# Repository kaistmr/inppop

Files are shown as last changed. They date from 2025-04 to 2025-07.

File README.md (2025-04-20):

# 인형뽑기 repository
이는 2025년도 태석제 및 캄프를 위한 인형뽑기 제작을 위한 사이드 프로젝트이다.

## 멤버
- 전체 팀장: **노경민**
- 하드웨어 팀: **노경민**, 전재원, 김희태, 류호현, 김준홍, 이명제, 이지후, 정용환
- 전장 및 전산 팀: **안연수**, 전재원, 이지후, 송민준

## 플젝 기간
|기간|활동|
|--|--|
|2025.03.16.|내부 회의 및 플젝 시작|
|2025.04.22.|pcb 테스트 및 코딩 진행|
|2025.05.03.|하드웨어 제작 완료|
|2025.05.13.-15.|태울석림제에서 시연 진행|

## 안내사항
기존 2025년도에 제작하여 주문한 pcb에서는 아두이노 메가 프로 부분에서의 GND 통일이 되어있지 않았다는 실수를 발견하여, 이를 점퍼를 이용해서 이어줌.
추후 다시 만든 manufacturing 파일은 문제 없는 상태이지만 2025버전을 사용할 때는 이를 유의해야 함.

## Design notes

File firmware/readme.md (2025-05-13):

# Firmware
- 최종 사용 코드 : `ard_nano.ino`, `mega.ino`
- 중간중간에 요소들 테스트는 `./test_elements` 폴더 속 파일들을 이용.
- 참고로 못 쓰게 된 핀도 많으니까 유의해서 코드 보기.

## Arduino nano
### Distance Sensing
- 핀: A7과 D2핀을 사용.
- 센서: distance sensor 사용
- 목적: 동전 투입구에 사용. 거리값이 일정한 상태에서 거리값이 줄어들어 동전 투입이 인식되면 대기 시퀀스에서 게임 시작 시퀀스로 변경
- 예제 코드: `./test/distance_sensor_test`

### mp3 module
- 핀: D6과 D12를 이용해 rx, tx 통신을 사용
- 모듈: DFPlayer mini를 활용
- 작동:
  - 대기 시퀀스: 폴더 하나(A) 속 노래를 랜덤하게 재생. 이 과정에서 폴더 내부 노래는 무한 반복
  - 게임 시작 시퀀스: 다른 폴더(B) 내부의 노래를 순차적으로 재생. 폴더 내부 노래는 무한 반복
- 통신 방식:
  - 직접 시리얼 통신을 통한 제어
  - 10바이트 명령어 패킷 사용 (SOF, VI, DL, CMD, ACK, DH, DL, CHL, CHH, EOF)
  - 체크섬을 통한 데이터 무결성 검증
  - 주요 명령어:
    - 0x0F: 음악 재생
    - 0x06: 볼륨 설정
    - 0x0C: 모듈 리셋
  - 초기화 순서:
    1. 모듈 리셋
    2. 볼륨 설정
    3. 음악 재생 시작
- 예제 코드: `./test/mp3_test`

## Arduino mega
### motor control
- 1번 모터(x축)
  - 모터 종류: DC모터
  - 모터 연결 핀: Signal(D40), Motor Control(D36, D38)
- 2번 모터(y축)
  - 모터 종류: DC모터
  - 모터 연결 핀: Signal(D41), Motor Control(D37, D39)
  - **주의사항** : 이 핀들은 이미 만들어진 보드에서 작동하지 않음. 따라서 외부 L298N을 사용해야 함. 혹은 z축 핀을 y축에 활용하고 3번 모터는 서보모터를 활용하는 것도 방법... (쓴다면 D35 핀을 사용)
- 3번 모터(z축)
  - 모터 종류: DC모터
  - 모터 연결 핀: Signal(D46), Motor Control(D42, D44)
  - 제어 방식: L298N을 활용한 제어. 적당히 감고, 적당히 푸는 능력이 중요
- 4번 모터(그리퍼)
  - 모터 종류: servo모터
  - 모터 연결 핀: D34 핀을 이용한 제어
  - 제어 방식: 최소 각도와 최대 각도를 정하고, 이를 반복하는 방식
- 리밋스위치
  - D9, D11, D15, D17을 이용해 x축의 +-, y축의 +- 최대치를 판별, z축의 경우 D19을 이용.
  - **주의사항** : D13번 핀은 왜인지 모르겠지만 작동하지 않음. 따라서 이를 제외하고 사용해야 함!
- 예제 코드: `./test/limit_switch_test`, `./test/motor_only_test`

### control input
- 조이스틱: 리밋스위치가 총 4개인 버전. D23, D25, D27, D29를 통해 값이 들어오며, 이를 바탕으로 x, y 축 이동
- 푸쉬버튼:
  - D31을 통해 리밋스위치 방식으로 값이 들어옴.
  - 버튼이 눌릴 시 dc 모터로 z축을 내린 뒤, 그리퍼로 늘렸다가 오므린 뒤, 다시 z축을 높히고, 원점으로 이동 후 그리퍼 펼치기 작업 실행.
  - 이 버튼이 눌린다면 게임 종료 시퀀스로 돌입.
- 예제 코드: `./test/joystick_button_test`

## Signal Pin(mega and nano)
- 핀(nano): D8(DigitalWrite)과 D3(DigitalRead)을 사용
- 핀(mega): D3(DigitalRead)와 D5(DigitalWrite)을 사용
- nano의 D8과 mega의 D3, nano의 D3과 mega의 D5는 서로 이어져 있음.
- 작동:
  - 동전이 투입된 이후 게임 시작 시퀀스 돌입시, arduino nano의 D8의 state를 1로 세팅.
  - Arduino mega의 D3 쪽에서 이를 인식 후, Mega의 D5을 1로 세팅하여 게임을 진행.
  - 게임이 끝나면 mega의 D5 값이 0으로 바뀌며, mini의 D3핀이 연결된 핀이 0 값을 read.
  - D3 핀에서 0 값이 인식되면 D8의 값을 0으로 내리며 하나의 과정 종료.
  - 이를 반복

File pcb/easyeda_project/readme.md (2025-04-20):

# PCB files 수정사항

|날짜|제목|수정사항|
|--|--|--|
|2025.3월|1차 pcb 제작|최대한 범용성 넓게 쓰기 위한 것을 목표로 제작|
|2025.04.21.|GND 수정|아두이노 메가의 GND가 통일되어있지 않음을 발견하여 수정|

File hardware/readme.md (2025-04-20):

# Hardware
이 공간은 하드웨어 관련 설계 파일이 올라갈 예정입니다.

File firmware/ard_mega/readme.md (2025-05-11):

- 하고자 하는 방향이었지만, 뭔가 잘 안되는 거 때문에 인터럽트를 적게 사용하고, 하는 방향으로 수정.
- **여기 폴더의 코드는 사용하지 않습니다**

## 핀맵
### communication
- nano로부터의 receive: D3(interrupt)
- nano로의 send: D5
- 여기서 게임 기회: `coin`

### control
- x+: D23(PA1)
- x-: D25(PA3)
- y+: D27(PA5)
- y-: D29(PA7)
- push: D31, D3(interrupt)

### limit
- x+: D9(PH6)
- x-: D11(PB5)
- y+: D15(PJ0)
- y-: D17(PH0)
- z: D19(PD2)
- 닿았을 때 flag: `stop_motor_z`

### origin point
- `x- & y+` 위치
- 원점 이동하라는 flag: `gohome`

## logic(loop)
if(`grip`)
if(`gohome`)
joy to move

### joy to move
- joy 값을 read
- 이거를 (x+, x-, y+, y-)에 대한 값으로 변경
  - 0: move
  - 1: don't move
- limit에 대한 값도 동일하게 가져오기(닿으면 0)
- joy(x+, x-, y+, y-)와 limit(x+, x-, y+, y-)의 값을 각 파트에 대해서 not(joy) and limit 적용한 거를 최종 모터에 전달
- 전달 받은 값 (x+, x-, y+, y-) 에 대한 값을 모터에 적용해서 움직임 진행

### push to grip
- push 버튼의 값이 인식되면, 모든 움직임 멈추기, `grip` flag 를 변화

### gohome
- `gohome` flag 값이 1이면 실행하는 거
- 무조건 왼쪽 상단으로 움직이기
- 그리퍼 열고 닫기
- 리밋 스위치 값 다 들어오면 `gohome` flag를 0으로 되돌리기

### grip
- `grip` flag가 들어오면 실행
- 그리퍼 열고
- z축 내리고
- 그리퍼 닫고
- z축 리밋 닿을 때까지 올리고
- `gohome` flag 1로 변화
- 1 `coin` 사용하기

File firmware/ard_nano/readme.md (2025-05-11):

## arduino nano 코드 구조
1. 2개의 상태가 존재: 동전 대기 / 게임 진행
2. 동전 대기:
- mp3 모듈에서 1번 폴더 속 노래를 랜덤하게 반복 재생
- distance 센서 인식 중
- 신호를 송신 받는 8번 핀이 LOW로 설정
3. 동전 대기 -> 게임 진행
- distance 센서 인식(D2) ; 인터럽트
- D8을 HIGH로 설정
- 만약 D7에 값이 HIGH가 들어오면 게임 진행 시퀀스로 돌입
4. 게임 진행:
- mp3 모듈에서 2번 폴더 속 노래를 랜덤하게 반복 재생
- 지속적으로 D7 핀에서 신호 수신(defalt: HIGH)
5. 게임 진행 -> 동전 대기
- D7 핀에 LOW 신호가 수신되면 D8 핀의 값도 LOW로 설정
- 다시 동전 대기 시퀀스 돌입

### 노래 개수
- 1번 폴더: 001-134
- 2번 폴더: 001-084

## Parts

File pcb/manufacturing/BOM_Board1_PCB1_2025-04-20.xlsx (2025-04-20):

No. | Quantity | Comment | Designator | Footprint | Value | Manufacturer Part | Manufacturer | Supplier Part | Supplier
1 | 1 | 100nF | C1 | CAP-SMD_L3.2-W1.6-RD | 100nF | CA45-A-35V-0.1UF-K | CEC(振华新云) | C2976900 | LCSC
2 | 2 | 220nF | C2,C3 | C0603 | 220nF | CC0603JRX7R6BB224 | YAGEO(国巨) | C519555 | LCSC
3 | 1 | 100nF | C4 | C0603 | 100nF | C0603X104K050T | IHHEC(禾伸堂) | C187860 | LCSC
4 | 2 | 220uF | C5,C6 | CAP-TH_BD8.0-P3.50-D0.6-FD | 220uF | HG1H227M0816PC | HONOR(荣誉) | C5438873 | LCSC
5 | 3 | BM04B-GHS-TBT(LF)(SN) | CN3,CN4,CN26 | CONN-SMD_4P-P1.25_BM04B-GHS-TBT-LF-SN |  | BM04B-GHS-TBT(LF)(SN) | JST | C161692 | LCSC
6 | 16 | BM02B-GHS-TBT(LF)(SN) | CN5,CN6,CN10,CN13,CN14,CN15,CN16,CN17,CN18,CN19,CN20,CN21,CN22,CN23,CN24,CN25 | CONN-SMD_2P-P1.25_BM02B-GHS-TBT-LF-SN |  | BM02B-GHS-TBT(LF)(SN) | JST | C161690 | LCSC
7 | 3 | KF141R-2.54-3P | CN7,CN27,CN28 | CONN-TH_3P-P2.54_KF141R-2.54-3P |  | KF141R-2.54-3P | KEFA(科发) | C475125 | LCSC
8 | 6 | KF141R-2.54-2P | CN8,CN9,CN31,CN32,CN33,CN34 | CONN-TH_2P-P2.54_KF141R-2.54-2P |  | KF141R-2.54-2P | KEFA(科发) | C475124 | LCSC
9 | 1 | XT60PW-M | CN35 | CONN-TH_XT60PW-M |  | XT60PW-M | AMASS(艾迈斯) | C98732 | LCSC
10 | 2 | DB141R-2.54-12P-GN | CN36,CN37 | CONN-TH_12P-P2.54_DIBO_DB141R-2.54-12P |  | DB141R-2.54-12P-GN | DORABO(地博电气) | C2898763 | LCSC
11 | 16 | 1N5819WS | D9,D10,D11,D12,D13,D14,D15,D16,D17,D18,D19,D20,D21,D22,D23,D24 | SOD-323_L1.8-W1.3-LS2.5-RD |  | 1N5819WS | Hottech(合科泰) | C191023 | LCSC
12 | 2 | PZ254V-11-22P | H1,H2 | HDR-TH_22P-P2.54-V-M |  | PZ254V-11-22P | XFCN(兴飞) | C22465881 | LCSC
13 | 2 | PZ254V-11-16P | H3,H4 | HDR-TH_PZ254V-11-16P |  | PZ254V-11-16P | XFCN(兴飞) | C22465876 | LCSC
14 | 1 | 2Ω | R1 | R0603 | 2Ω | SCR0603J2R | VO(翔胜) | C3017797 | LCSC
15 | 2 | 47kΩ | R2,R3 | R0603 | 47kΩ | 0603WAJ0473T5E | UNI-ROYAL(厚声) | C25600 | LCSC
16 | 2 | 10kΩ | R4,R5 | R0603 | 10kΩ | AT0603BRD0710KL | YAGEO(国巨) | C723396 | LCSC
17 | 1 | ARDUINO_NANO | U1 | COMM-TH_ARDUINO_NANO |  | ARDUINO_NANO |  | C9900017879 | LCSC
18 | 1 | DFplayer | U6 | DFplayer
19 | 1 | 1000uF | U7 | CAP-TH_BD12.5-P5.00-D0.6-FD | 1000uF | 35YXF1000MEFC12.5X25 | rubycon(红宝石) | C439893 | LCSC
20 | 1 | TDA7297 | U8 | MULTIWATT-15_L19.6-W5.0-P1.27-L |  | TDA7297 | ST(意法半导体) | C96009 | LCSC
21 | 1 | 10uF | U9 | CAP-SMD_BD4.0-L4.3-W4.3-LS5.0-FD | 10uF | VT10UF16V167RV0128 | KNSCHA(科尼盛) | C5246581 | LCSC
22 | 2 | PZ254V-11-15P | U10,U11 | HDR-TH_15P-P2.54-V-M |  | PZ254V-11-15P | XFCN(兴飞) | C22465875 | LCSC
23 | 1 | 470uF | U12 | CAP-SMD_BD6.3-L6.6-W6.6-LS7.2-FD | 470uF | RST470UF10V029 | KNSCHA(科尼盛) | C4747954 | LCSC
24 | 1 | ARD_MEGA2560PRO | U13 | COMM-SMD_L54.0-W38.0-P2.54_ARD_MEGA2560PRO |  | ARD_MEGA2560PRO |  | C9900135944 | LCSC
25 | 2 | L298N | U14,U15 | MULTIWATT-15_L19.6-W5.0-P1.27-L |  | L298N | ST(意法半导体) | C19922 | LCSC
26 | 2 | KH-SS22D07-VG4H | U16,U17 | SW-TH_KH-SS22D07-VG4H |  | KH-SS22D07-VG4H | kinghelm(金航标) | C5274482 | LCSC

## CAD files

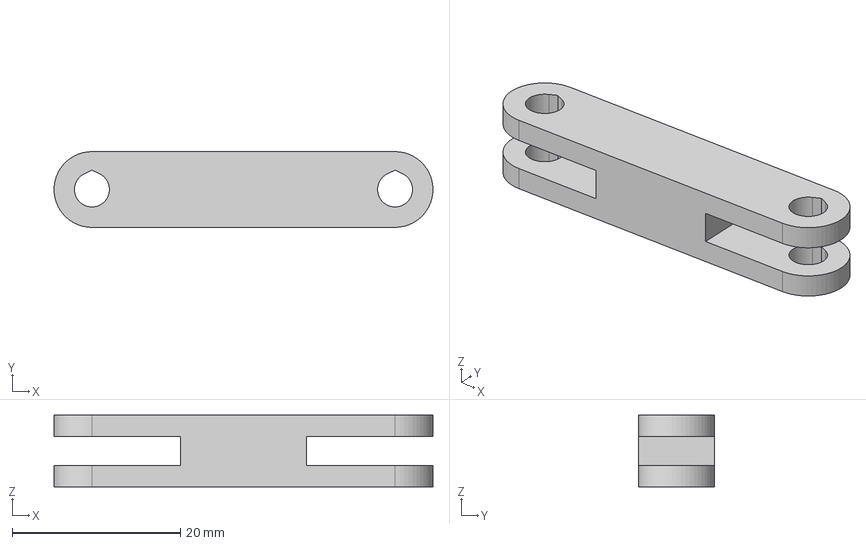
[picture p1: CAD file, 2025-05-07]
hardware/Claw STEP files/Part H v6.step
45.0 x 9.00 x 8.50 mm

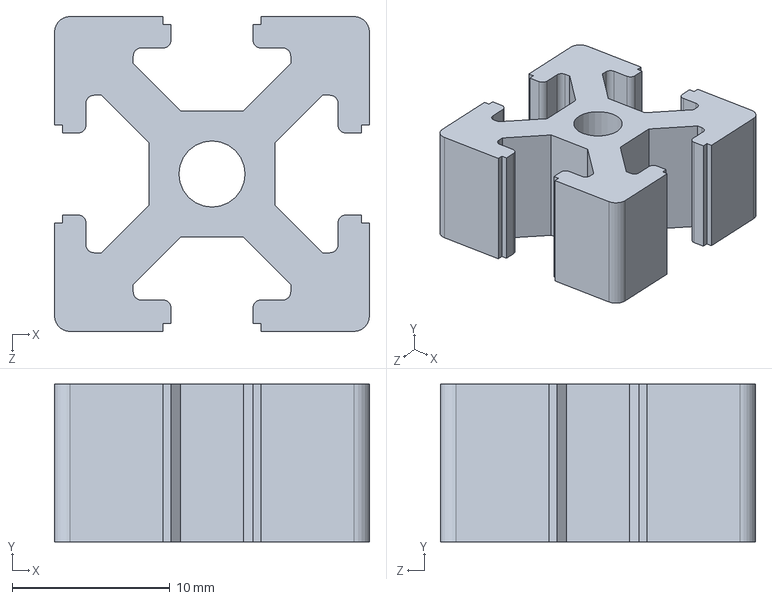
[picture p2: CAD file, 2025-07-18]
hardware/main/new/2020profile.SLDPRT
20.0 x 10.0 x 20.0 mm

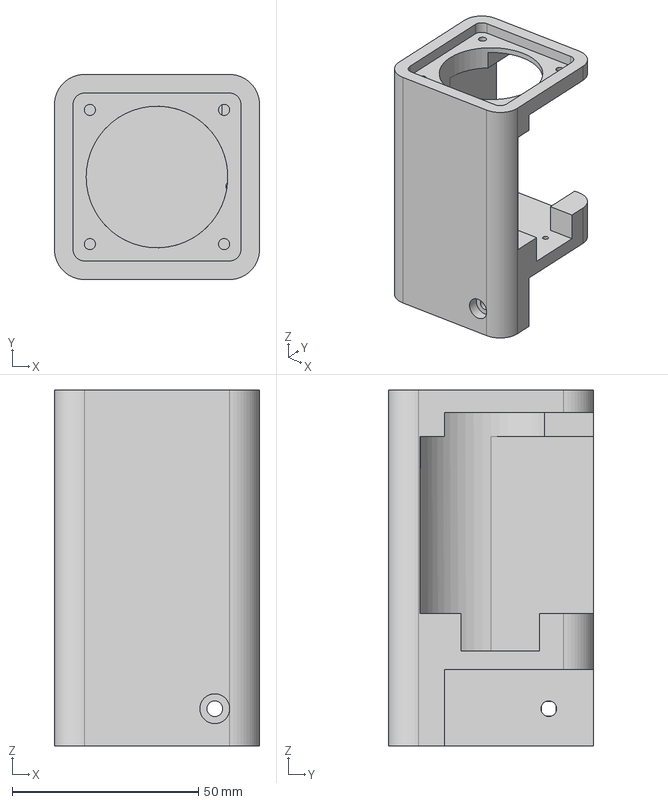
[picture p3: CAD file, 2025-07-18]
hardware/main/ver1/motor-profile connector R.step
55.0 x 55.0 x 95.5 mm

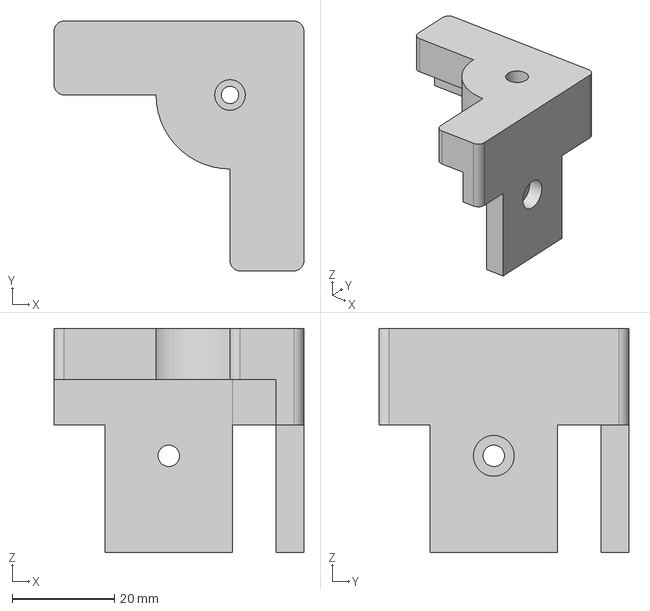
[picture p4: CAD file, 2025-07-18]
hardware/main/ver1/idler-profile connector 2.step
49.0 x 49.0 x 44.0 mm

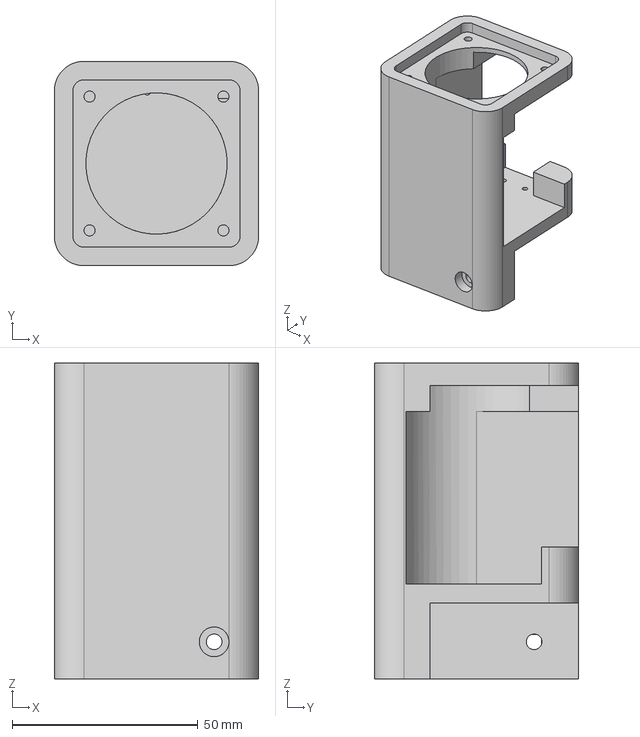
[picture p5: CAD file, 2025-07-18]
hardware/main/ver1/motor-profile connector L.step
55.0 x 55.0 x 85.0 mm

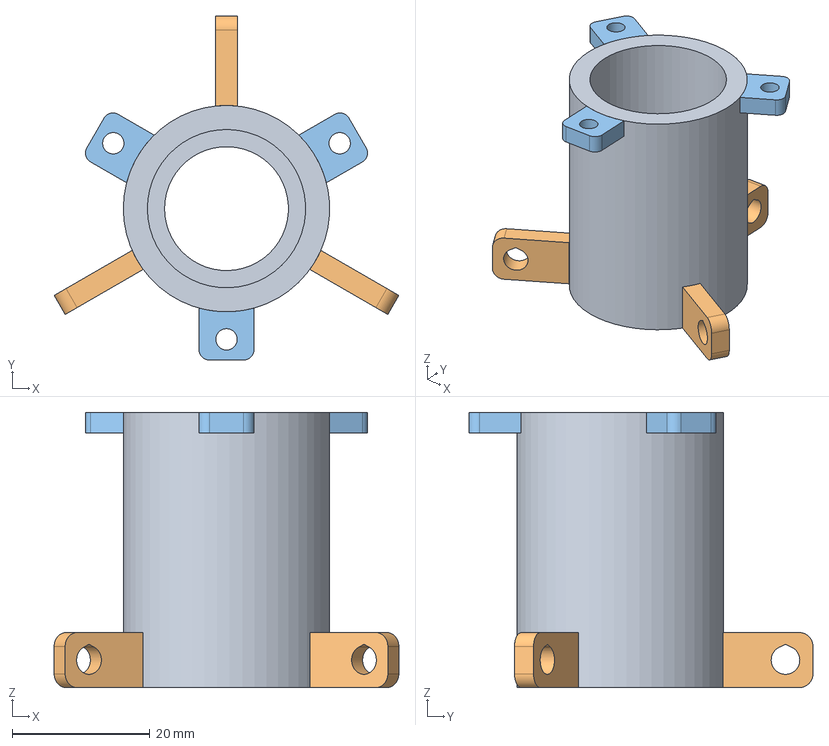
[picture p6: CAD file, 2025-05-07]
hardware/Claw STEP files/Cylinder v7.step
50.1 x 50.0 x 40.0 mm

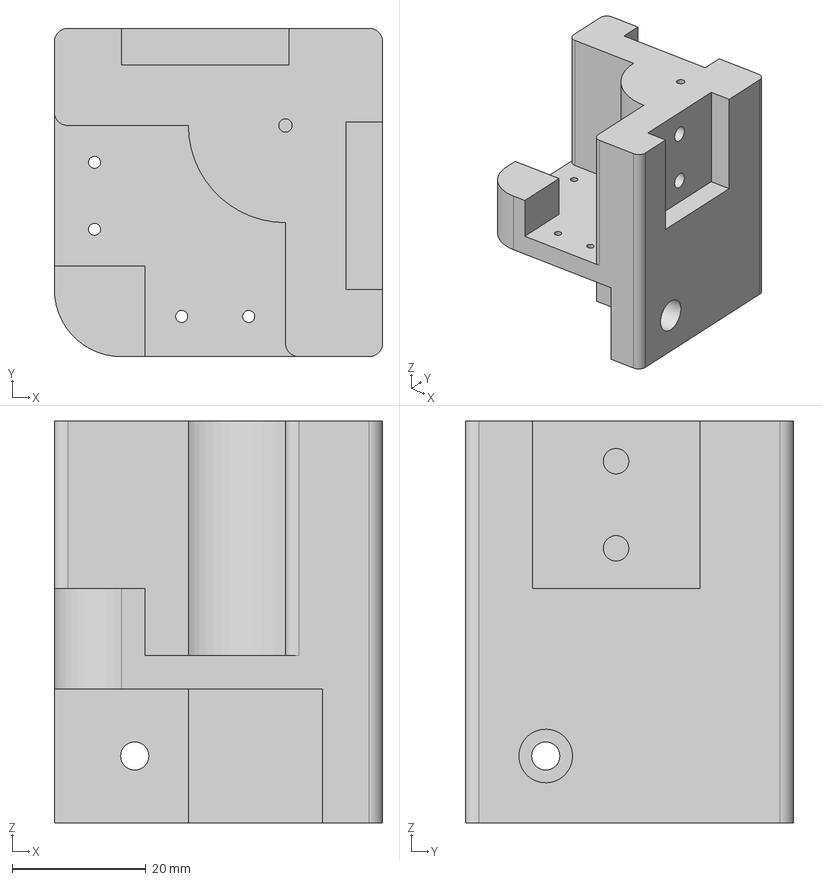
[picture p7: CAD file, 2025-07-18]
hardware/main/ver1/idler-profile connector 1.step
49.0 x 49.0 x 60.0 mm

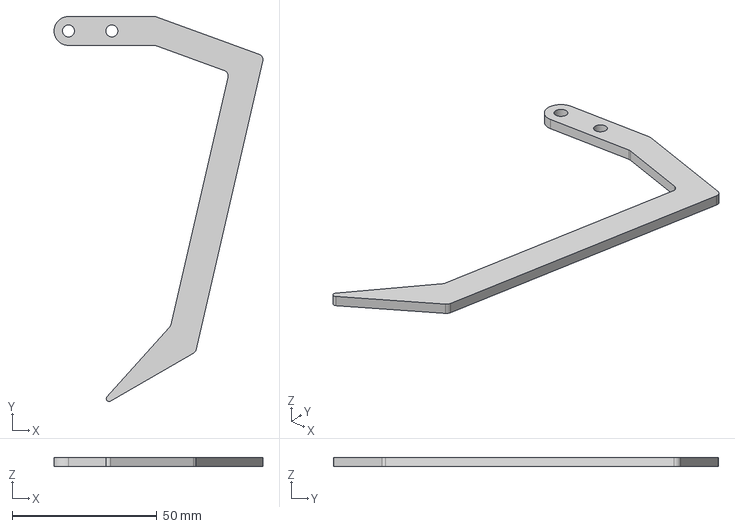
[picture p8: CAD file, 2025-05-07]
hardware/Claw STEP files/Claw v8.step
72.2 x 133.1 x 3.20 mm

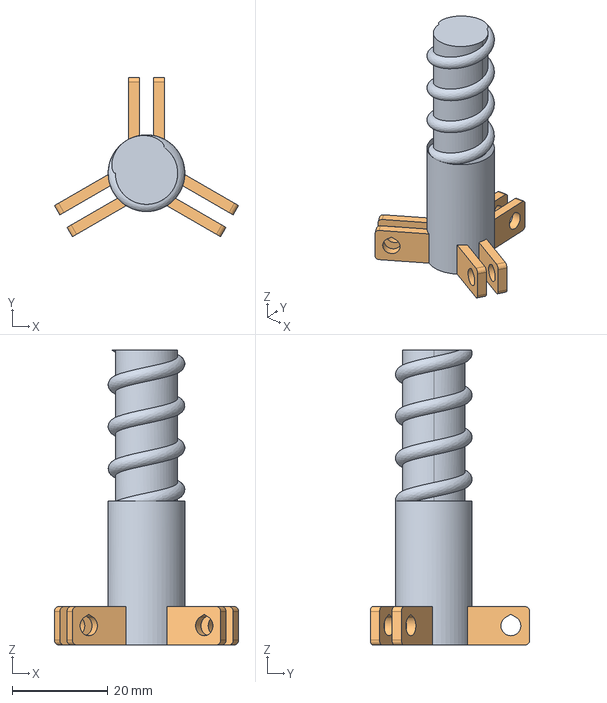
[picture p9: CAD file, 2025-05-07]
hardware/Claw STEP files/Bolt v5.step
38.4 x 33.2 x 61.5 mm

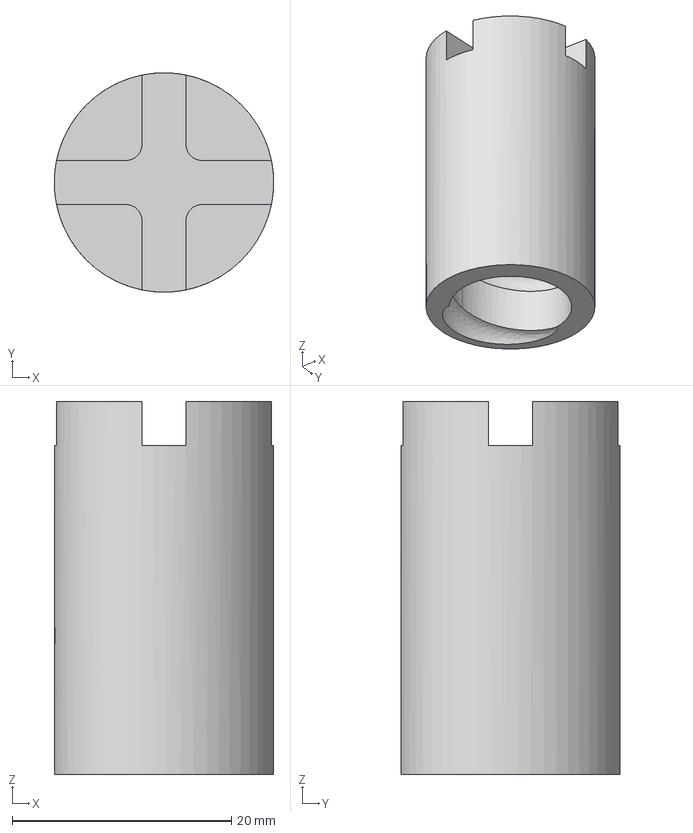
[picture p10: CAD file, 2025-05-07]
hardware/Claw STEP files/Nut v4.step
20.0 x 20.0 x 34.0 mm

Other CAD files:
hardware/main/ver1/Untitled v8.f3d
hardware/main/ver1/idler-profile connector 1.f3d
hardware/main/ver1/idler-profile connector 2.f3d
hardware/main/ver1/main v17.f3d
hardware/main/ver1/motor-profile connector L.f3d
hardware/main/ver1/motor-profile connector R.f3d

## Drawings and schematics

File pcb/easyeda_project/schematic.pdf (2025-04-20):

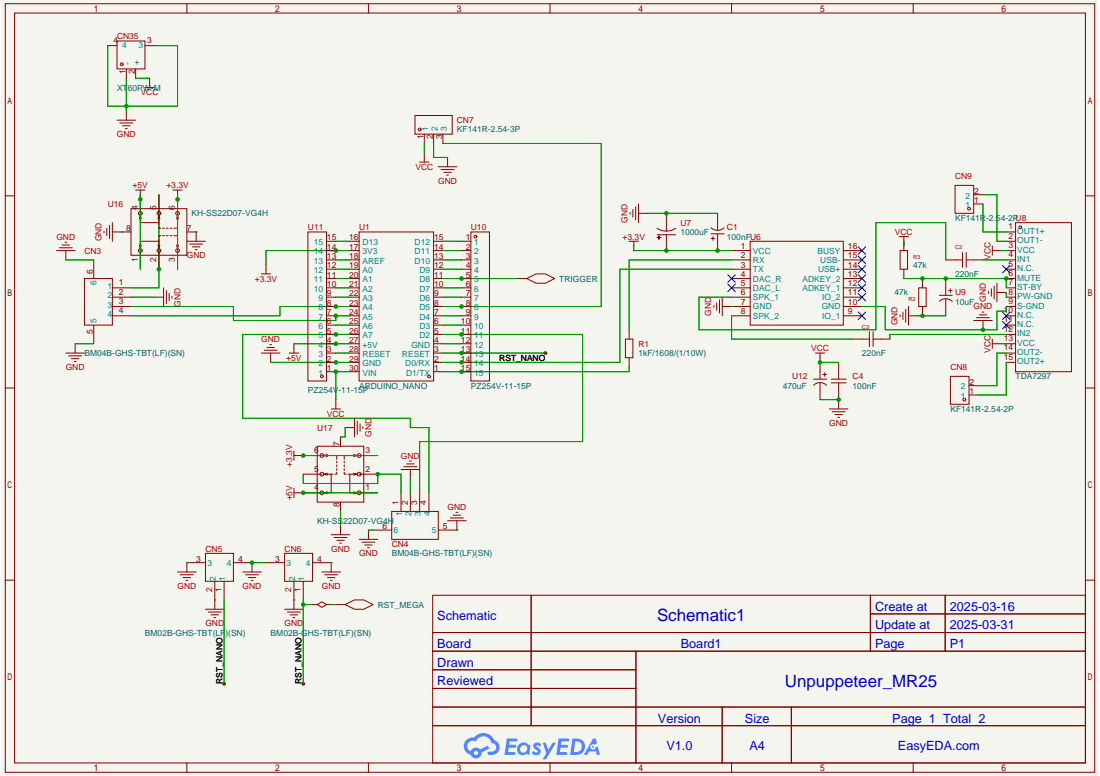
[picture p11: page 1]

GND 10 IO_2 11 ADKEY_1 12 ADKEY_2 13 USB+ 14 USB- 15 BUSY 16

Schematic | Schematic1 | Create at | 2025-03-16

Update at | 2025-03-31

BM02B-GHS-TBT(LF)(SN)

Board | Board1 | Page | P1
Drawn | | Unpuppeteer_MR25
Reviewed

Version | Size | Page 1 Total 2
V1.0 | A4 | EasyEDA.com

D31 21 | D30 22 D28 23 D26 24 D24 25 D22 26 D20 27 D18 28 D16 29 D14 30 D12 31 D10 32 D8 33 D6 34 D4 35 D2 36 RX 37 REF 38 3.3V 39 5V 40 GND 41 VIN 42
D47 64 | D46 65 D44 66 D42 67 D40 68 D38 69 D36 70 D34 71 D32 72 A14 73 A12 74 A10 75 A8 76 A6 77 A4 78 A2 79 A0 80

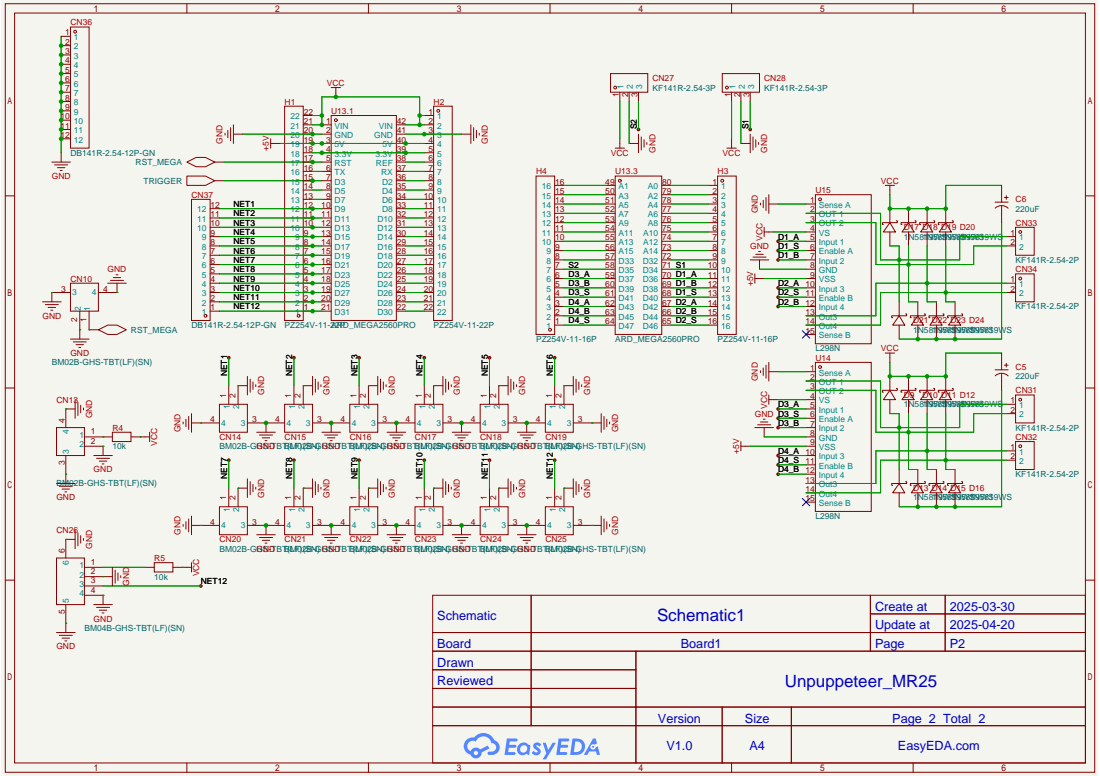
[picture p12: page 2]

GND
BM02B-GHS-TBT(LF)(SN)

Schematic | Schematic1 | Create at | 2025-03-30

Update at | 2025-04-20

Board | Board1 | Page | P2
Drawn | | Unpuppeteer_MR25
Reviewed

Version | Size | Page 2 Total 2
V1.0 | A4 | EasyEDA.com

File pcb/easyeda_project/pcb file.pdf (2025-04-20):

# GND 12V

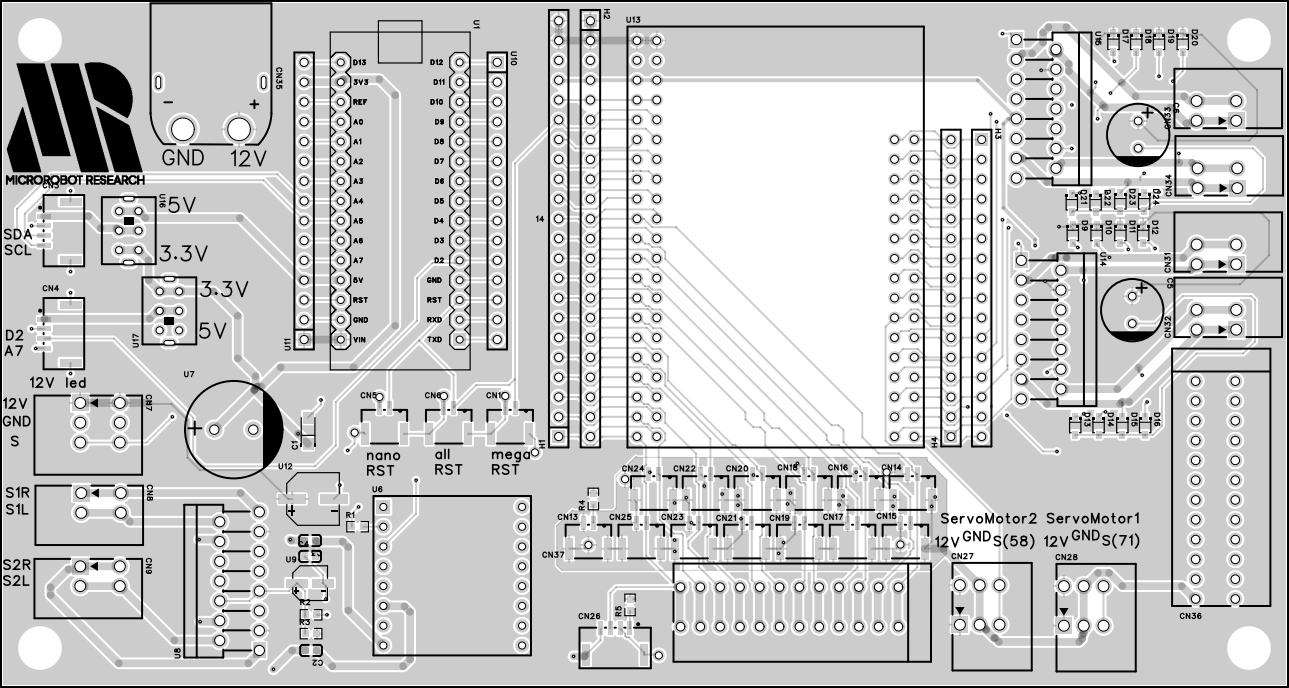
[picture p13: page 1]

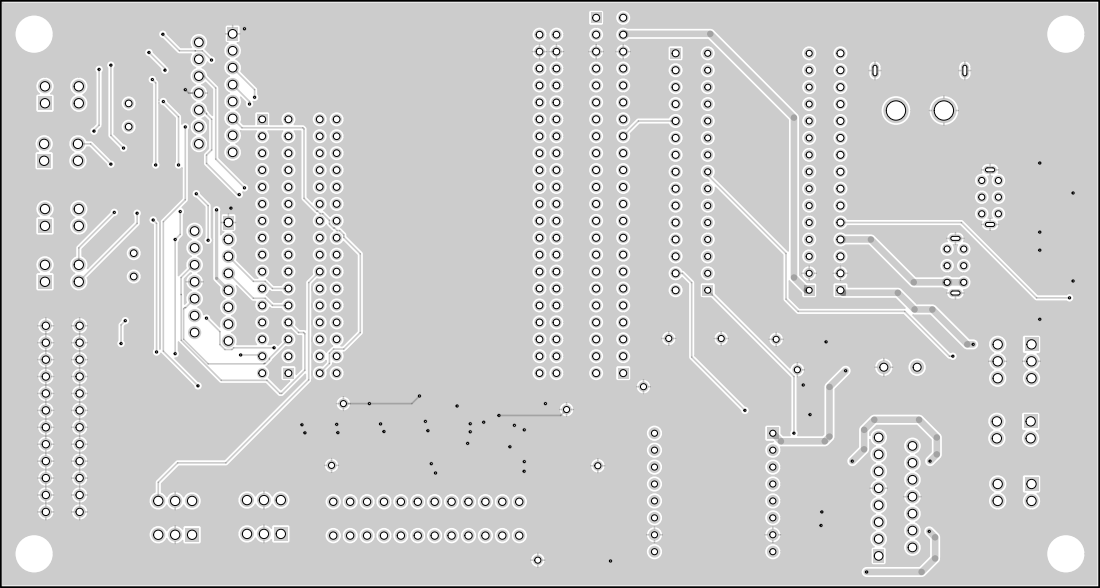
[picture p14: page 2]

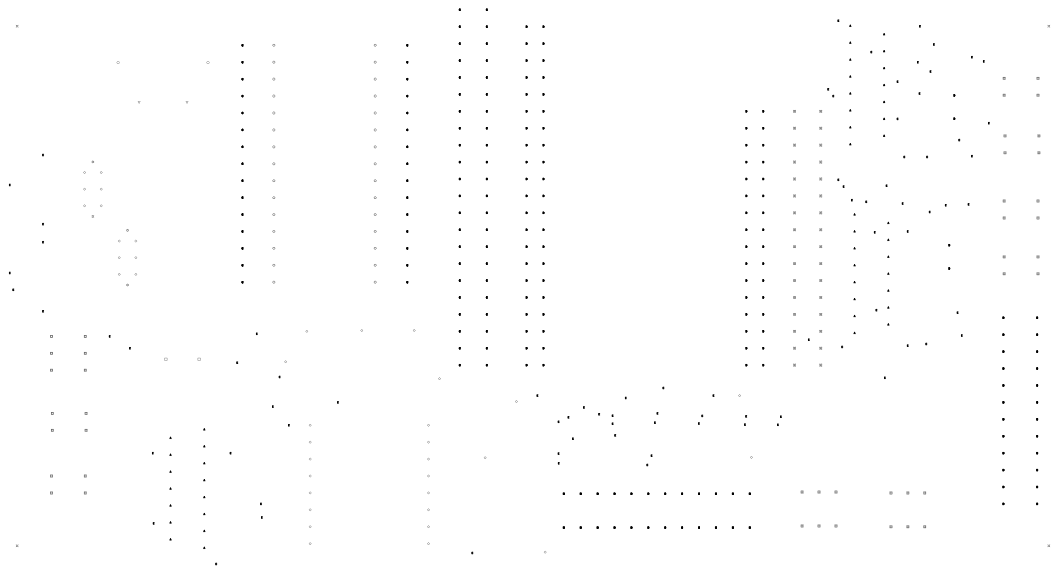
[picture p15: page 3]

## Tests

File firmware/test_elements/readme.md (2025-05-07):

# Arduino Mega 테스트 코드 모음

이 폴더는 Arduino Mega의 각 기능을 개별적으로 테스트하기 위한 코드들을 포함하고 있습니다.

## 테스트 코드 목록

### 1. 모터 테스트 (motor_only_test)
- 모터의 기본 동작 테스트
- X, Y, Z축 모터 개별 제어
- 모터 방향 및 속도 제어 확인

### 2. 리밋 스위치 테스트 (limit_switch_test)
- 각 축의 리밋 스위치 동작 확인
- X+, X-, Y+, Y-, Z축 리밋 스위치 상태 모니터링
- 시리얼 모니터를 통한 실시간 상태 확인

### 3. 조이스틱 & 버튼 테스트 (joystick_button_test)
- 조이스틱 입력 테스트
- X+, X-, Y+, Y- 방향 입력 확인
- 조이스틱 버튼 동작 확인
- 시리얼 모니터를 통한 실시간 상태 모니터링

### 4. 모터 & 리밋 스위치 통합 테스트 (motor_limit_test)
- 모터와 리밋 스위치 연동 테스트
- 리밋 스위치 동작 시 모터 정지 기능 확인
- 안전 기능 테스트

### 5. 거리 센서 테스트 (distance_sensor_test)
- 초음파 거리 센서 동작 확인
- 거리 측정 정확도 테스트
- 시리얼 모니터를 통한 거리 값 확인

### 6. MP3 모듈 테스트 (mp3_test)
- DFPlayer Mini MP3 모듈 동작 테스트
- 음악 재생, 정지, 볼륨 제어 기능 확인
- 시리얼 모니터를 통한 제어

## 사용 방법
1. Arduino IDE를 실행합니다.
2. 테스트하고자 하는 기능의 .ino 파일을 엽니다.
3. 코드를 Arduino에 업로드합니다.
4. 시리얼 모니터(115200 baud)를 열어 테스트 결과를 확인합니다.

## 주의사항
- 각 테스트 코드는 독립적으로 동작하도록 설계되어 있습니다.
- 테스트 전 반드시 하드웨어 연결을 확인하세요.
- 시리얼 모니터를 통해 동작 상태를 실시간으로 모니터링할 수 있습니다.
- 문제 발생 시 각 테스트 코드의 주석을 참고하세요.

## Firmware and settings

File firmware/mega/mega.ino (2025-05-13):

#include <Servo.h>

const int X_MOTOR[3] = {41, 37, 39};
const int Y_MOTOR[3] = {40, 36, 38};
// const int Z_MOTOR[3] = {47, 43, 45};
const int Z_PIN = 47;
const int GRIP_PIN = 35;

// 조이스틱 핀
const int JX_P = 23;
const int JX_M = 25;
const int JY_P = 27;
const int JY_M = 29;
const int BTN = 31;

// 리밋 스위치 핀
const int LX_P = 21;
const int LX_M = 11;
const int LY_P = 15;
const int LY_M = 17;
const int LZ = 19;

// 통신 핀
const int COMM_OUT = 5;
const int COMM_IN = 2;

// 모터 제어
const int MOTOR_SPEED = 255;  // 모터 속도 (0-255)
const int GRIP_SPEED = 220;  // z축 모터 속도 (0-255)
const unsigned long MOTOR_TIMEOUT = 1000;  // 모터 타임아웃 (ms)
const int GRIP_OPEN = 1000; // 그리퍼 열림 값
const int GRIP_CLOSE = 1900; // 그리퍼 닫는 값
 const int GRIP_STOP = 1450; // 그리퍼 멈춤
const int Z_DOWN = 1900;
const int Z_UP = 1000;
const int Z_STOP = 1450;
Servo grip;
Servo z_axis;

// flag 설정
int state = 0; //0: 대기, 1: 움직임
int gamecoin = 0;

void COIN_ISR()
{
  gamecoin++;
}

void MotorSetup(const int pins[3])
{
  pinMode(pins[0], OUTPUT);
  pinMode(pins[1], OUTPUT);
  pinMode(pins[2], OUTPUT);
  digitalWrite(pins[0], LOW);
}

void MotorMove(const int pins[3], int dir, int vel)
{
  if (dir > 0)
  {
    digitalWrite(pins[1], HIGH);
    digitalWrite(pins[2], LOW);
    analogWrite(pins[0], vel);
  } else if (dir < 0) {
    digitalWrite(pins[2], HIGH);
    digitalWrite(pins[1], LOW);
    analogWrite(pins[0], vel);
  } else {
    digitalWrite(pins[0], LOW);
  }
}

bool reachlimit(const int limit_pin)
{
  return !digitalRead(limit_pin);
}

void gohome(const int x_axis_motor[3], const int y_axis_motor[3], const int grip_pin, const int limit_x, const int limit_y)
{
  bool x_reach = false;
  bool y_reach = false;

  while(!x_reach || !y_reach)
  {
    x_reach = reachlimit(limit_x);
    y_reach = reachlimit(limit_y);
    !x_reach ? MotorMove(x_axis_motor, 1, MOTOR_SPEED) : MotorMove(x_axis_motor, 0, 0);
    !y_reach ? MotorMove(y_axis_motor, 1, MOTOR_SPEED) : MotorMove(y_axis_motor, 0, 0);
  }
  MotorMove(x_axis_motor, 0, 0);
  MotorMove(y_axis_motor, 0, 0);
  if(gamecoin > 0)
  {
    grip.writeMicroseconds(GRIP_OPEN); // open
    delay(MOTOR_TIMEOUT);
    grip.writeMicroseconds(GRIP_STOP);
    delay(MOTOR_TIMEOUT);
    grip.writeMicroseconds(GRIP_CLOSE); // close
    delay(MOTOR_TIMEOUT);
    grip.writeMicroseconds(GRIP_STOP);
    delay(MOTOR_TIMEOUT);
  }
}

void setup()
{
  Serial.begin(9600);
  attachInterrupt(digitalPinToInterrupt(COMM_IN), COIN_ISR, RISING);

  MotorSetup(X_MOTOR);
  MotorSetup(Y_MOTOR);
  // MotorSetup(Z_MOTOR);
  grip.attach(GRIP_PIN);
  z_axis.attach(Z_PIN);

  pinMode(BTN, INPUT_PULLUP);
  pinMode(LX_P, INPUT_PULLUP);
  pinMode(LX_M, INPUT_PULLUP);
  pinMode(LY_P, INPUT_PULLUP);
  pinMode(LY_M, INPUT_PULLUP);
  pinMode(LZ, INPUT_PULLUP);
  pinMode(JX_P, INPUT_PULLUP);
  pinMode(JX_M, INPUT_PULLUP);
  pinMode(JY_P, INPUT_PULLUP);
  pinMode(JY_M, INPUT_PULLUP);

  pinMode(COMM_OUT, OUTPUT);
  pinMode(COMM_IN, INPUT);

  grip.writeMicroseconds(GRIP_OPEN); // open
  delay(MOTOR_TIMEOUT);
  grip.writeMicroseconds(GRIP_STOP);
  delay(MOTOR_TIMEOUT);
  grip.writeMicroseconds(GRIP_CLOSE); // close
  delay(MOTOR_TIMEOUT);
  grip.writeMicroseconds(GRIP_STOP);
  delay(MOTOR_TIMEOUT);
  z_axis.writeMicroseconds(Z_STOP);
  delay(5000);
  gamecoin = 0;
}

void loop()
{
  Serial.print("gamecoin: ");
  Serial.print(gamecoin);
  Serial.print("  state: ");
  Serial.println(state);

  if(reachlimit(BTN))
  {
    MotorMove(X_MOTOR, 0, MOTOR_SPEED);
    MotorMove(Y_MOTOR, 0, MOTOR_SPEED);
  //  MotorMove(Z_MOTOR, -1, GRIP_SPEED);
    z_axis.writeMicroseconds(Z_STOP);
  //  MotorMove(Z_MOTOR, 0, 0);
    grip.writeMicroseconds(GRIP_OPEN);
    delay(MOTOR_TIMEOUT);
    grip.writeMicroseconds(GRIP_STOP);
    delay(MOTOR_TIMEOUT);
    z_axis.writeMicroseconds(Z_DOWN);
    delay(2000);
    z_axis.writeMicroseconds(Z_STOP);
    delay(500);
    grip.writeMicroseconds(GRIP_CLOSE);
    delay(MOTOR_TIMEOUT);
    grip.writeMicroseconds(GRIP_STOP);
    delay(MOTOR_TIMEOUT);
    z_axis.writeMicroseconds(Z_UP);
    delay(2000);
    /*
    while(!reachlimit(LZ))
    {
      MotorMove(Z_MOTOR, 1, GRIP_SPEED);
      delay(1000);
    } */
    z_axis.writeMicroseconds(Z_STOP);
    // MotorMove(Z_MOTOR, 0, 0);
    gohome(X_MOTOR, Y_MOTOR, GRIP_PIN, LX_M, LY_P);
    gamecoin--;
    digitalWrite(COMM_OUT, HIGH);
    delay(1000);
    digitalWrite(COMM_OUT, LOW);
  }
  if(!state)
  {
    gohome(X_MOTOR, Y_MOTOR, GRIP_PIN, LX_M, LY_P);
    MotorMove(X_MOTOR, 0, MOTOR_SPEED);
    MotorMove(Y_MOTOR, 0, MOTOR_SPEED);
    if(gamecoin > 0)
    {
      state = 1;
    }
  }
  if(state && (gamecoin > 0))
  {
    if(reachlimit(BTN)) return;

    int order_x = reachlimit(JX_P) - reachlimit(JX_M);
    int order_y = reachlimit(JY_P) - reachlimit(JY_M);

    if(reachlimit(LX_M) && reachlimit(JX_P)) order_x = 0;
    if(reachlimit(LX_P) && reachlimit(JX_M)) order_x = 0;
    if(reachlimit(LY_P) && reachlimit(JY_P)) order_y = 0;
    if(reachlimit(LY_M) && reachlimit(JY_M)) order_y = 0;

    MotorMove(X_MOTOR, order_x, MOTOR_SPEED);
    MotorMove(Y_MOTOR, order_y, MOTOR_SPEED);
  }
}

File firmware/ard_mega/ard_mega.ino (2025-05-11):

// core xy에서 x축 y축으로 변경
// 하나하나 체크하면서 이동관련해서 코드 짜야 함.
// 기존의 코드를 이용해서 코드 참고해서 짜도 좋을듯?

#include "motor_control.h"
#include "limit_switch.h"
#include <Servo.h>

// 모터 핀
const int L_MOTOR[3] = {40, 36, 38};
const int R_MOTOR[3] = {41, 37, 39};
const int Z_MOTOR[3] = {47, 43, 45};
const int GRIP_PIN = 35;

// 조이스틱 핀
const int JX_P = 25;
const int JX_M = 23;
const int JY_P = 29;
const int JY_M = 27;
const int BTN = 31;

// 리밋 스위치 핀
const int LX_P = 21;
const int LX_M = 11;
const int LY_P = 17;
const int LY_M = 15;
const int LZ = 19;

const int COMM_OUT = 5;
const int COMM_IN = 2;

#define CW 1
#define CCW 0

// 게임 상태
enum GameState {
  WAIT,    // 대기 상태
  PLAY,    // 게임 진행 중
  DONE     // 게임 종료
};

// 그리퍼 상수
const unsigned long G_DELAY = 5000;  // 5초
const unsigned long G_ACT = 2000;     // 1.5초
const int G_OPEN = 100;
const int G_CLOSE = 80;

// 모터 제어 상수
const int MOTOR_SPEED = 200;  // 모터 속도 (0-255)
const int GRIP_SPEED = 100;  // z축 모터 속도 (0-255)
const unsigned long MOTOR_TIMEOUT = 5000;  // 모터 타임아웃 (ms)

// 객체 생성
MotorControl L_M(L_MOTOR);
MotorControl R_M(R_MOTOR);
MotorControl Z_M(Z_MOTOR);
LimitSwitch lx_p(LX_P);
LimitSwitch lx_m(LX_M);
LimitSwitch ly_p(LY_P);
LimitSwitch ly_m(LY_M);
LimitSwitch lz(LZ);
Servo Grip;

GameState state = WAIT;
bool btn_pressed = false;
bool is_start = false;
int gamecoin = 0;

void COIN_ISR() {
  gamecoin++;
  digitalWrite(COMM_OUT, HIGH);
}

void moveHome() {
  bool x_reached = false;
  bool y_reached = false;

  while(!x_reached || !y_reached)
  {
    // X축 이동 (X- 리밋 스위치로)
    if (!x_reached) {
      if (lx_m.isLimitTriggered()) {
        x_reached = true;
        L_M.stop();
        R_M.stop();
      } else {
        L_M.move(-1, MOTOR_SPEED);
        R_M.move(-1, MOTOR_SPEED);
      }
    }

    // Y축 이동 (Y+ 리밋 스위치로)
    if (!y_reached) {
      if (ly_m.isLimitTriggered()) {
        y_reached = true;
        L_M.stop();
        R_M.stop();
      } else {
        L_M.move(-1, MOTOR_SPEED);
        R_M.move(1, MOTOR_SPEED);
      }
    }
    delay(10);
  }

  L_M.stop();
  R_M.stop();
}

void gamePlay() {
  if (btn_pressed) return;

  // 조이스틱 입력 읽기
  int jx = digitalRead(JX_M)-digitalRead(JX_P);
  int jy = digitalRead(JY_M)-digitalRead(JY_P);

  // 리밋 스위치 체크
  if (lx_p.isLimitTriggered() && jx > 0) jx = 0;
  if (lx_m.isLimitTriggered() && jx < 0) jx = 0;
  if (ly_p.isLimitTriggered() && jy > 0) jy = 0;
  if (ly_m.isLimitTriggered() && jy < 0) jy = 0;

  // 모터 제어
  int l_dir = jx + jy;
  int r_dir = jx - jy;

  L_M.move(l_dir, MOTOR_SPEED);
  R_M.move(r_dir, MOTOR_SPEED);
}

void gripMove() {
  // Z축 하강
  analogWrite(47, 255);
  digitalWrite(43, HIGH);
  digitalWrite(45, LOW);
  delay(1000);
  analogWrite(47, 0);
  digitalWrite(43, HIGH);
  digitalWrite(45, LOW);
  delay(1000);

  // 그리퍼 동작
  Grip.write(G_OPEN);
  delay(G_ACT);
  Grip.write(G_CLOSE);
  delay(G_ACT);

  // Z축 상승
  while(!lz.isLimitTriggered())
  {
    analogWrite(47, 255);
    digitalWrite(43, LOW);
    digitalWrite(45, HIGH);
  }
}

void setup() {
  Serial.begin(115200);
  Serial.println("로봇 제어 시스템 초기화 중...");

  attachInterrupt(digitalPinToInterrupt(COMM_IN), COIN_ISR, RISING);

  // 모터 및 조이스틱 초기화
  L_M.setup();
  R_M.setup();
  Z_M.setup();

  // 리밋 스위치 초기화
  lx_p.setup();
  lx_m.setup();
  ly_p.setup();
  ly_m.setup();
  lz.setup();

  // 조이스틱 핀 설정
  pinMode(BTN, INPUT_PULLUP);
  pinMode(JX_P, INPUT_PULLUP);
  pinMode(JX_M, INPUT_PULLUP);
  pinMode(JY_P, INPUT_PULLUP);
  pinMode(JY_M, INPUT_PULLUP);

  // 그리퍼 초기화
  Grip.attach(GRIP_PIN);
  Grip.write(G_OPEN);
  delay(1000);

  Serial.println("초기화 완료!");
  gamecoin = 0;
  delay(1000);
}

void loop() {
  Serial.print("gamecoin: ");
  Serial.println(gamecoin);

  // 버튼 상태 확인 (LOW가 눌림 상태)
  bool btn_state = !digitalRead(BTN);
  if (btn_state && !btn_pressed) {
    btn_pressed = true;
    L_M.stop();
    R_M.stop();
    Z_M.stop();
  }

  if(gamecoin > 0) {
    state = PLAY;
  }

  switch (state) {
    case WAIT:
      if (!is_start) {
        moveHome();
        Serial.println("초기 위치로 이동 완료");
      }
      break;

    case PLAY:
      gamePlay();
      if (btn_pressed) {
        gripMove();
        moveHome();
        btn_pressed = false;
        state = DONE;
        Serial.println("게임 종료!");
      }
      break;

    case DONE:
      moveHome();
      Serial.println("새 게임 준비 완료");
      state = WAIT;
      is_start = false;
      gamecoin--;
      digitalWrite(COMM_OUT, LOW);
      break;
  }
}

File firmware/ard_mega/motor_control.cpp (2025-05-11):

#include "motor_control.h"

MotorControl::MotorControl(const int pins[3])
    : enablePin(pins[0]), dir1Pin(pins[1]), dir2Pin(pins[2]), isEnabled(false) {}

void MotorControl::setup() {
  pinMode(dir1Pin, OUTPUT);
  pinMode(dir2Pin, OUTPUT);
  pinMode(enablePin, OUTPUT);

  digitalWrite(enablePin, LOW);  // 초기 상태는 비활성화
  isEnabled = true;
}

void MotorControl::move(int direction, int vel) {
  if (!isEnabled) return;

  if (direction > 0) {
    digitalWrite(dir1Pin, HIGH);
    digitalWrite(dir2Pin, LOW);
    analogWrite(enablePin, vel);
  }
  else if (direction < 0) {
    digitalWrite(dir2Pin, HIGH);
    digitalWrite(dir1Pin, LOW);
    analogWrite(enablePin, vel);
  }
  else {
    stop();
  }
}

void MotorControl::stop() {
  digitalWrite(enablePin, LOW);
}

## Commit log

2025-04-20 first commit of project. upload init files
    [BOM_Board1_PCB1_2025-04-20.xlsx, PickAndPlace_PCB1_2025-04-20.xlsx]
2025-04-29 조이스틱 제어 및 리미트 스위치 기능을 위한 인터럽트 기반 업데이트 구현. 펌웨어 문서 및 테스트 가이드 추가.
2025-05-01 Add files via upload
    인형뽑기 집게 STEP 파일
    [Bolt v5.step, Claw v8.step, Cylinder v7.step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]
2025-05-08 펌웨어 업데이트: 조이스틱 및 모터 제어 기능 개선, 리미트 스위치 테스트 코드 추가, 전체적인 코드 구조 정리 및 주석 추가.
2025-05-08 펌웨어 업데이트: 거리 센서 및 MP3 플레이어 기능 개선, 통신 상태 디바운싱 추가, 초기화 및 게임 상태 관련 로그 출력 추가.
2025-05-09 펌웨어 수정: ard_mega.ino 그리퍼 동작 시간 조정 및 모터 속도 변경, 리미트 스위치 체크 방식 개선.
    [ard_mega.ino]
2025-05-09 펌웨어 수정: ard_mega.ino에서 그리핑 상태 변수 제거 및 코드 정리.
    [ard_mega.ino]
2025-05-10 펌웨어 수정: 거리 센서 및 MP3 플레이어 코드 개선, 초기화 및 통신 관련 기능 추가, 코드 구조 정리 및 주석 보강.
    [ard_nano.ino, ard_nano_test.ino, distance_sensor.cpp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]
2025-05-11 펌웨어 수정: ard_nano.ino에서 동전 감지 및 음악 재생 기능 개선, 통신 핀 변경 및 코드 구조 정리. 사용하지 않는 파일 삭제.
    [ard_mega.ino, ard_mega_fixed.ino, ard_nano.ino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]
2025-05-12 continuous servo 모터로 교체
2025-05-13 제발리드미읽어
